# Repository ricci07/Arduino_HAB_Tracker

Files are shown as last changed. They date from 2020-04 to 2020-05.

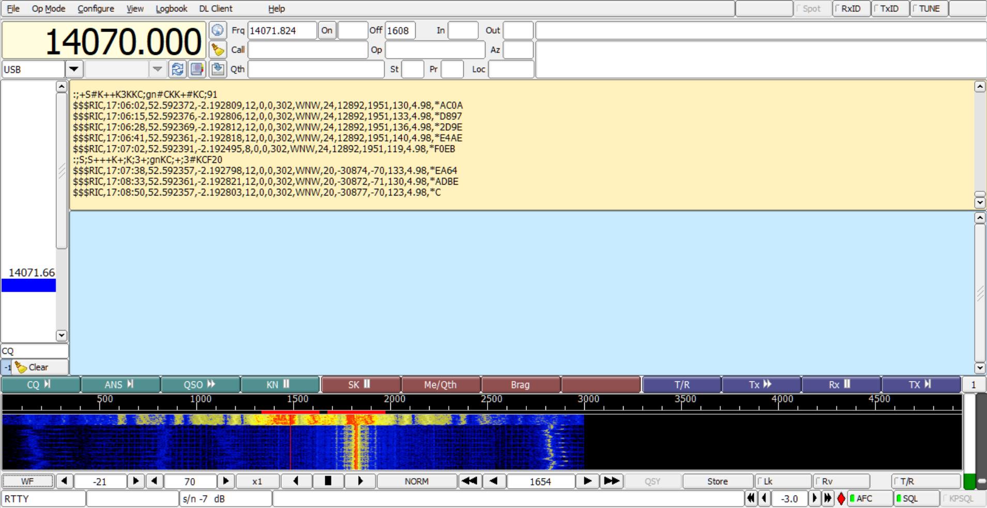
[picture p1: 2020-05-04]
Screenshot/Thesis/DL-Fldigi showing RTTY lesser unwanted tone oscillation when connected to external 3V with external ground and arduino ground linked.jpg

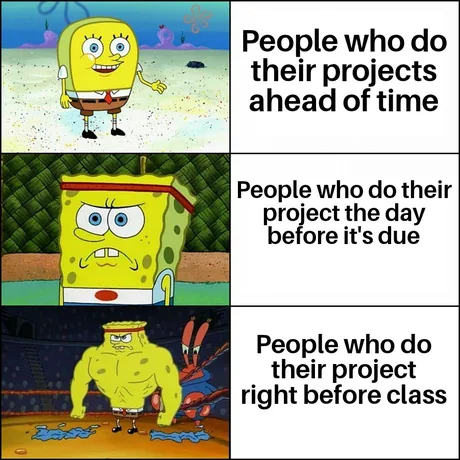
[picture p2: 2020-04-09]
Proposal/project.webp

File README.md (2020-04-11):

# Arduino_HAB_Tracker
Undergraduate Dissertation HAB Telemetry Development

This is a HAB tracker PCB I am making for my final year project based on information provided by the UKHAS (society)
I am building this from breakout boards, which is not my preferred solution, but it will speed up developement 10-fold (I don't have the time for anything pretty right now)

It features an Arduino UNO (clone), Ublox-M8Q (GPS) Radiometrix NTX2B, BH1750 (light sensor), BMP280 (pressure sensor), ML8511 (UV sensor), MPU-9250 (9 Axis Sensor, 3D acc, 3D GYR, 3D Mag), MS5611 (Super-high alitude sensor), and voltage sensor (this consists of a voltage divider so many be implemented directly)

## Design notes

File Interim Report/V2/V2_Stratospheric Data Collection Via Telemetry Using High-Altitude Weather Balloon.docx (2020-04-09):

# Stratospheric Data Collection via Telemetry Using High-Altitude Weather Balloon

Interim Report

by Riccardo Geraci

Friday, 24 January 2020

# 1 Abstract

Weather balloons are an invaluable tool used professionally by meteorology organisations for collecting various types of atmospheric data used in forecasting the weather. This includes collecting things such as atmospheric pressure, humidity, and temperature. Outside of the professional sector they are highly used by radio amateurs to gather sensor data and photos and videos of the Earth’s curvature. The types of sensor data commonly collected by amateurs are from a 3-axis accelerometer, 3-axis gyroscope, 3-axis magnetometer, relative humidity, altitude, temperature, pressure, ambient light, and ultraviolet light. These are then transmitted to ground via the onboard telemetry via the 70cm 434MHz HAM band to a computer connected to a radio receiver, DVB-T dongle, Funcube+ dongle, or airspy which is tuned to 434Mhz. The main tracking computer is usually run inside a chase car with a magnetically mounted 70cm band antenna. The GPS location of the balloon is broadcasted the same way as the sensor data with the coordinates acquired from an onboard GPS module connected to low orbit satellites. A service called habhub is used by the majority to allow anyone around the world to track the balloon. This has the advantage of filling in any signal loss you may encounter since someone else is relaying the coordinates to the server for you. Balloons of various sizes, commonly between 300-600g for first time launchers ascend until a point (usually 60,000-120,000ft depending on the balloon size, with larger more expensive ones achieving higher altitudes) where the air pressure is so low (about 0.1 atmospheres) which causes the balloon to expand until rupturing. At this point the payload containing the electronics descend with a legally required parachute somewhere near a previously software predicted landing location. This is commonly between 2-3 hours away from the launch location. Lots of preparation is done to ensure the prediction is not in the ocean. Though prediction algorithms aren’t perfect, and the weather has tendency to change unpredictably so the landing location prediction needs constant rerunning to ensure the most updated location is known.

Ukhas.org (UK high altitude society) is the single most abundant and reliable source of high-altitude ballooning on the internet with veteran members creating articles which instruct others how to launch a balloon of their own. These members have been approached by organisations such as the BBC to fabricate and launch balloons for TV and have helped myself in this project with direct correspondence or through their articles. Credit will be paid to them where appropriate in interim or dissertation. Without their contributions this project would have not been possible to carryout due to its complexity.

# 2 Introduction

# 3 Design Constraints

## 3.1 Altitude

The burst altitude is dependent on various factors such as the size of the balloon, payload weight, and rate of ascent. Common 600g Totex balloons have a burst altitude of between 75,000 - 90,000ft whereas larger and more expensive balloons (800g-4000g) have a larger gas capacity and extended amount of stretch than smaller ones (100-600g). So, they have a longer time of ascent, hence altitudes of beyond 90,000ft can be achieved (Kaymont.com, 2020). For this project a 600g will be used as it is the most commonly used latex balloon for first time launchers and can be purchased from Steve Randall’s website; randomengineering.co.uk for ≈£25

## 3.2 Launch

In the UK, permission must be obtained prior to launch from the Civil Aviation Authority (CAA) before any weather balloons can be launched. An OS map pinpointing the planned launch location must be sent before permission is granted. If valid, permission and a NOTAM (notice to airmen) will be issued. Due to unpredictable weather a window of different launch dates should be requested. 28 days prior notice must be given before planned launch date (Stirk, 2012).

## 3.3 Location

## 3.4 Software Defined Radio

Software defined radio is an inexpensive alternative to using an expensive but also more sensitive radio such as the most commonly used Yaesu 817. SDR dongles utilise the Realtek RTL2832U chipset and computer’s soundcard to decode radio signals. However, SDR dongles are repeatedly discouraged for tracking actual balloon flights due to their reduced sensitivity when compared to a proper radio. Although, this argument is conflicted by different people and a compromise has to be taken.

## 3.5 Tracking

After launching of the balloon, a chase car with a magnetically roof mounted 70cm band antenna connected with a length of SMA terminated RG174 cable is fed to and usb dvb-t dongle connected to a computer running sdrsharp software tuned to ≈ 434.425MHz, the same as the payload transmitting frequency. The received RTTY tones are then sent to dl-fldigi software via a virtual audio cable where the tones are decoded in sentences containing the GPS coordinates of the balloon’s current position. This GPS information is then relayed to habhub to allow worldwide tracking of the balloon (Stirk, 2012).

## 3.6 Flight Computer

Original plans were to use the raspberry pi as per mentioned by Heather Lomond Ph.D, a member of TDARS amateur radio group I attended as per suggestion of Mohammad Sayed. The raspberry pi allows the use of the pi camera which could have programmed to take photos every x seconds. Heather has launched two weather balloons before and shared her story of how she achieved it. She mentioned she used the pi-in-the-sky flight tracker developed by Dave Akerman. This is a tracker that is pre-made by one of the expert HAB members to slot on the top of raspberry pi. However, due to price of £144, an ambitious decision to develop my own flight tracker was made.

## 3.7 GPS

The GPS module chosen for this project is the uBlox Max-M8Q. This is the most commonly used GPS chip used by the HAB community because it continues to operate up to 50,000 meters when in flight mode. Not all GPS modules continue to work at this altitude and result in monotonic values. This ensures the balloon’s location doesn’t go silent when the balloon goes beyond the operating altitude (uBLOX MAX-M8Q Breakout for Active Antennas, 2016).

## 3.8 Balloon

A 600g Totex balloon from randomengineering.co.uk is going to be used to carry a payload of 500-900g

## 3.9 Size

## 3.10 Payload

## 3.11 Gas

## 3.12 Transmitter

## 3.13 Parachute

## 3.14 Power Supply

## 3.15 Regulations

## 3.16 CAA Limitations

## 3.18 SDR

## 3.19 Budget

## 3.20 Sensors

## 3.21 9 Axis Sensor

## 3.22 Talk about the 3 axis acceleraomter, 3 axis gyroscope, and 3 axis magnometer.

## 3.23 Ambient Light Sensor (GY-302)

## 3.24 Talk about how the light sensor will be used to record the light level increase/decreate during the flight of the ballon

## 3.25 UV Light Sensor (GY-8511)

## 3.26 Talk about how the light sensor can track the uv levels during ascent and decent which we can parse the data to create graphs in excel

## 3.27 Altitude Sensor & 9 Axis Sensor (MS5661 & MPU-9250)

## 3.28 Talk about how the bmp280 stop function beyond certain altitude (60,000ft/10hPa), but the MS5661 works up to 100,000ft/ 1hPa which is required to allow for no monotonic values beyond that point

## 3.29 Voltage Sensor

## 3.30 Talk about how the voltage sensor can be used to monitor the battery percentage and so that we can look at how to battery level went down during the flight of the balloon.

## 3.31 Printed Circuit Board (PCB)

# 4 References

Kaymont.com. (2020). [online] Available at: https://www.kaymont.com/product-page/hab-600 [Accessed 24 Jan. 2020].

Stirk, A. (2012). general:restrictions_legality [UKHAS Wiki]. [online] Ukhas.org.uk. Available at: https://ukhas.org.uk/general:restrictions_legality [Accessed 24 Jan. 2020].

Stirk, A. (2012). guides:sdr_tracker [UKHAS Wiki]. [online] Ukhas.org.uk. Available at: https://ukhas.org.uk/guides:sdr_tracker [Accessed 24 Jan. 2020].

uBLOX MAX-M8Q Breakout for Active Antennas. (2016). [ebook] Bingley: uputronics, p.2. Available at: https://store.uputronics.com/files/HAB-BO-M8Q3A-ASSY.pdf [Accessed 24 Jan. 2020].

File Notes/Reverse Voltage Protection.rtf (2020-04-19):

Reverse Voltage Protection

There are many ways to provide voltage protection to a circuit

• Series diode after power source (Basic, not great, alot of wasted heat)

• Series shotkey diode after power source (Better, less heat wasted but still not the ultimate method). A shotkey diode has a lower forward voltage.

• P-channel mosfet with Drain conected in series with the positive supply and the source connected to the load (Absolute best way)

Wasted heat calculation

Forward Voltage x Current = Wasted Power

How much is too much wasted heat?

Anything approaching 2W is on the high side.
A max of 1W or below is preferrable.

Which diode?

P/N 1N4001 [1]

Which Shotkey diode?

P/N MBRA130 [1] or STPS2L60 (0.55V forward voltage) [2]

Which P-channel Mosfet?

FQP47P06 [2]
• Pay attention to the unconvention pin configuration of this mosfet

How to wire the p-channel mosfet [2]
• The drain-source voltage rating must be higher than the psu voltage [2]
• Rds(on) should be as low as possible to minimize the resitive power losses [2]
• Get one with a high gate-source voltage (+-25v) [2]

• The mosfet is parasitic so there is a 1V volt-drop across (D)rain and (S)ource [2].
• This means the (S)ource pin is at 11V w.r.t GND [2]
• The gate voltage is 0V because it is connected to GND [2]

How to deal with voltages higher than gate-source voltage range
• Use a resistor and zener diode (1N5240) (10V) in this configuration [2]
• A zener between 6-12V should be adequate [2]

References

[1] https://www.allaboutcircuits.com/technical-articles/how-to-protect-your-circuits-using-only-a-diode/

[2] https://www.youtube.com/watch?v=IrB-FPcv1Dc

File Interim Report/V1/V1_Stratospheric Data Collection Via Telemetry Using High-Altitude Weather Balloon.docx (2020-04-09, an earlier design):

# Stratospheric Data Collection via Telemetry Using a High-Altitude Weather Balloon

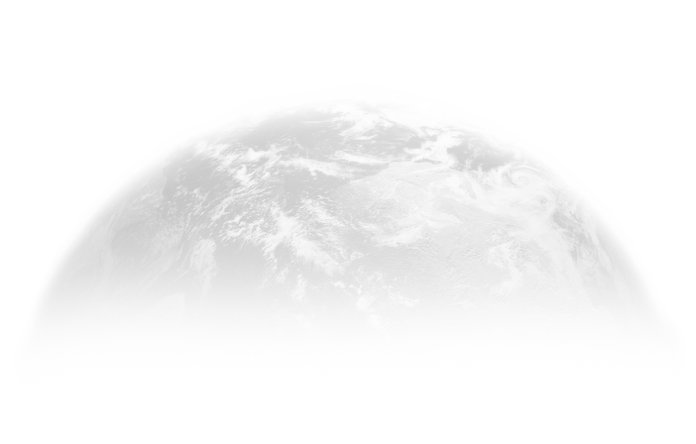
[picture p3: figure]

Interim Report

by Riccardo Geraci | 1615626

Friday, 14 February 2020

Supervised by Niki Zakeri

# 1 Abstract

Weather balloons are an invaluable tool used professionally by meteorology organisations for collecting various types of atmospheric data used in forecasting the weather. This includes collecting things such as atmospheric pressure, humidity, and temperature. Outside of the professional sector, they are highly used by radio amateurs to gather sensor data, photos, and videos of the Earth’s curvature.

The types of sensor data commonly collected by amateurs are via 3-axis accelerometers, 3-axis gyroscopes, 3-axis magnetometers, relative humidity sensors, pressure/altitude sensors, temperature sensors, ambient light sensors, and ultraviolet light sensors. These are then transmitted to the ground by telemetry via the 70cm 434Mhz HAM band to a computer connected to a radio receiver, DVB-T dongle, FUNcube Pro+ dongle, or Airspy – which is also tuned to 434Mhz with SDR tuning software in the case it’s a DVB-T dongle. The main tracking computer is typically running from inside a chase car with a magnetically roof-mounted 70cm band antenna. The GPS location of the balloon is transmitted the same way as the sensor data but with the coordinates acquired from an onboard GPS receiver connected to GPS satellites.

A service called HABhub is used by UKHAS to allow anyone around the world to track the balloon. This has an advantage of filling in any signal loss encountered by someone else relaying the GPS coordinates to the server.

Balloons of various sizes, commonly between 300-600g for first-time launchers, ascend at an ideal 5m/s until a point (usually 60,000-120,000ft depending on the balloon size and system mass, with larger and more expensive balloons achieving higher altitudes) where the air pressure is low enough (about 0.1 atmospheres) that the balloon expands to the point of rupturing. For a 600g balloon, this is 6.5m in diameter (Randall, 2019). For the best photographs of the Earth, an altitude of 25-30km/82,000-98,000ft is an ideal altitude to aim for (Akerman, 2015).

Following the balloon bursting, the payload containing the electronics descend with a legally required parachute at an ideal descent rate of 5m/s tuned by the size of the parachute selected, somewhere near a previously software predicted landing location. This is commonly between 2-3 hours away from the launch location. Lots of preparation is done to ensure the prediction is not in the ocean, airport, or restricted areas. Though prediction algorithms aren’t perfect, and the weather tends to change unpredictably, so the landing location prediction needs constant rerunning to ensure the most updated location is known.

From running several prediction tests, the average flight until the balloon bursts is usually 90-100 minutes, with a flight duration of approximately 120-130 minutes. See 3.12 - Provisional Flight Prediction to see information about this in more detail.

# 2 Introduction

This interim report introduces some of the research carried out from October 2019 to January 2020 in the development of a high-altitude weather balloon for obtaining sensor data from the stratosphere. The research includes learning how to build a flight tracker by interfacing a uBlox GPS chip with a microcontroller via UART serial and parsing the NMEA sentences and extracting the desired GPS coordinates and altitude. The tracker also includes a Radiometrix NXT2B which transmits the relevant sentences via traditional RTTY to the receiver antenna mounted on top a chase car. Other data protocols such as CW (Morse), DominoEX, and LoRa are also used instead of or in conjunction with RTTY and live in-flight images can be sent with SSTV (Coxon, 2020).

The majority of the research has come from Ukhas.org (UK high altitude society). They offer the single most abundant and reliable source of high-altitude ballooning on the internet with veteran members creating articles which instruct others how to launch a balloon of their own. These members have been approached by organisations such as the BBC to fabricate and launch balloons for TV and have helped directly in this project with one-to-one correspondence or through their public articles. Credit will be paid to them where appropriate in interim or dissertation. Without their contributions, this project would have not been possible to carry out due to its complexity.

The sensor modules were purchased in breakout board form with the intention of integrating them into a tracker PCB containing the other key components such as the Radiometrix NTX2B, SMA antenna connectors, and switch-mode voltage regulators. All the sensor boards use I2C to communicate with the microcontroller, which means the SDA and SCL lines will need to be interconnected with a BUS to pins A4 and A5 of the Arduino.

Switched-mode voltage regulators will be used to supply the various voltages from an external source required by the different sensors, such as 3.3v and 5v without putting too much strain on the Arduino supply.

The research into the parachute required, helium amount required, and which chase car antenna is required has been pushed towards the end of the research as it is dependent on the totals of other components. To ensure the correct parachute size is purchased or fabricated, the total mass of the system will need to be measured first to acquire an optimal descent rate/landing speed of 5m/s (Akerman, 2015).

To ensure to correct helium quantity is obtained, the system mass, balloon size, and target burst altitude/ascent rate need to be determined first. The parachute size can be determined once the system mass is measured.

# 3 Design Research

## 3.1 Budget

The budget for this project has been more expensive than anticipated. Many technical articles have quoted £200, which is quite underestimated. As of 26/01/20, not all items have been purchased and ≈ £300 has already been spent. After purchasing the remaining items, such as helium, laptop inverting charger, parachute, action camera, SD card, mag-mount antenna, and balloon, the expenses come to £498.55. This excludes ≈ £40 fuel costs to retrieve the payload upon landing 2-4 hours away depending on the effects of wind on the day of launch. Appendix A – Parts List and Project Budget shows the currently spent funds in obtaining the necessary equipment and parts.

## 3.2 Altitude

The burst altitude is dependent on various factors such as the size of the balloon, payload weight, and rate of ascent. Common 600g latex balloons have a burst altitude of between 75,000ft - 90,000ft (Kaymont.com, 2020) whereas larger and more expensive balloons (800g-4000g) have a larger gas capacity and extended amount of stretch than smaller ones (100g-600g). So, they have a longer time of ascent, hence altitudes of beyond 90,000ft can be achieved (Kaymont.com, 2020). For this project, a 600g-1000g balloon will likely be used as they are the most commonly used latex balloons for first-time launchers and can be purchased from Steve Randall’s website; randomengineering.co.uk for ≈£25

## 3.3 Launch

In the UK, permission must be obtained prior to launch from the Civil Aviation Authority (CAA) before any weather balloons can be launched. An OS map pinpointing the planned launch location must be sent before permission is granted. If valid, permission and a NOTAM (notice to airmen) will be issued. Due to unpredictable weather, a window of different launch dates should be requested. 28 days prior notice must be given before the planned launch date (Stirk, 2012).

## 3.4 Software Defined Radio

Software-defined radio is an inexpensive alternative to using an expensive but also more sensitive radio such as the most commonly used Yaesu 817. SDR dongles utilise the Realtek RTL2832U chipset and computer’s soundcard to decode radio signals. However, SDR dongles are repeatedly discouraged for tracking actual balloon flights due to their reduced sensitivity when compared to a proper radio. Although, this argument is conflicted by different opinions and a compromise has to be taken.

## 3.5 Tracking

After launching of the balloon, a chase car with a magnetically roof-mounted 70cm band antenna connected with a length of SMA terminated RG174 cable is fed to a USB DVB-T dongle connected to a computer running SDRsharp software tuned to ≈ 434.425MHz, the same as the payload transmitting frequency. The received RTTY tones are then sent to dl-fldigi software via a virtual audio cable where the tones are decoded character by character into sentences containing the GPS coordinates of the balloon’s current position. This GPS information is then relayed to HABhub to allow worldwide tracking of the balloon (Stirk, 2012). Once the balloon lands, the perfect line of sight is almost always lost, and usually the signal with it. It is recommended to use a YAGI antenna from this point since they are highly directional and can detect faint signals (Akerman, 2015). It’s best to drive around the predicted landing location with a YAGI antenna until the signal is re-established to locate the payload (Lomond, 2019).

## 3.6 Flight Computer

Original plans were to use the Raspberry Pi as per mentioned by Heather Lomond PhD, a member of TDARS amateur radio group recommended by Mohammad Sayed. The Raspberry Pi allows the use of the Pi camera which could have programmed to take photos every x seconds. Heather has launched two weather balloons before and shared her story of how she achieved it. She mentioned she used the pi-in-the-sky (PITS) flight tracker developed by Dave Akerman and Anthony Stirk. This is a tracker that is pre-made by two expert HAB members to sit on the top of the Raspberry Pi. However, due to the price of £144, an ambitious choice to develop a flight tracker was made.

A later decision came to switch to the Arduino since the Raspberry Pi in a UKHAS member’s own words is ‘hardly ideal as a flight controller’ due to requiring knowledge of running a real-time kernel, linking a c program, higher power consumption (5-10 times more than normal tracker), and has a limited about shields readily available, etc (Akerman, 2020). Most of the available sample code for GPS and RTTY transmission is written for Arduino and is difficult to reimplement in python for the Raspberry Pi without significant python knowledge.

## 3.7 GPS

The GPS module chosen for this project is the uBlox Max-M8Q. This is the most commonly used GPS chip used by the HAB community because it continues to operate up to 50,000 meters when in flight mode. Not all GPS modules continue to work at this altitude and result in monotonic values. This ensures the balloon’s location doesn’t go ‘silent’ when the balloon goes beyond the operating altitude (uBLOX MAX-M8Q Breakout for Active Antennas, 2016).

## 3.8 Balloon

A 600g Latex balloon from randomengineering.co.uk is going to be used to carry a payload of between 500g and 900g. The payload will need to carry 4-6 lithium AA batteries that serve as the power supply, microcontroller, tracker/sensors PCB, action camera, etc. The weight of the payload container, which is a 2.4L polystyrene box, parachute, connecting lines, and antenna, needs to be accounted for in the lifting capabilities of the balloon. The balloon has a burst diameter of 6.5m which is significantly larger than its diameter at launch (Randall, 2019).

Helium will be used as the lifting gas. It’s the most commonly used gas in HAB because it is safer to use than hydrogen and methane. Though hydrogen is cheaper and lighter (hence, has more lift) it is said to be explosive when mixed with the correct amount of air. Although, hydrogen also does not diffuse out of the balloon as quickly as helium (Coxon, 2009).

The Radiometrix NTX2B 434.425MHz 10mW transmitter is the proven workhorse of many trackers used by the HAB community. In fact, 10mW is the maximum operating power that can be used for licence-free transmission. This still allows several hundreds of miles of signal due to a perfect line of sight to the receiver when in the sky (Coxon, 2009). The transmitter is connected to a 50 Ω RG174 pigtail via an SMA connector. The antenna radiating element is cut to 164mm to achieve a ¼ wave. A 4-point radial of approximately 164mm is used to simulate a ground plane or counterpoise to increase the reflections of the radio signal (Coxon, 2014).

## 3.9 Parachute

The parachute is a requirement by the CAA to bring the payload and balloon remnants back to the ground safely. The size of parachute depends on the balloon’s post burst weight. Parachutes can be found cheaply ( ≈ £25), expensively ( ≈£65) , or can be made at home using a sewing machine and nylon sheeting. Nylon is used for its strength and resistance to the cold since the temperature in the stratosphere averages at about -50 ℃ (Coxon, J, 2009).

The balloon train must also be made of nylon, usually, 1mm braided as this provides enough strength but has a low enough breaking strain as required by the CAA (Lomond, 2019). 1mm braided nylon has a breaking strain of about 22.5KG/220N, however, it is not made to precise breaking strain (Randall, 2019).

## 3.10 Power Supply

The source of power for this purpose is to use disposable energiser lithium AA batteries as they are the most resilient to the cold ( -40^o C to +60^o C ) (Energizer, n.d.) and are energy-dense. 6 x 1.5V AA lithium will provide a 9V power supply which is expected to last around 5 hours when coupled with an appropriate switched-mode voltage regulator. However, this will depend on the total current draw from the components, which can be evaluated after the construction of all circuitry for a more accurate expected working time (Coxon, 2009). Adding another 6 in parallel will double the working time to about 10 hours (Akerman, 2015).

## 3.11 Sensors

The objective of launching a high-altitude balloon was to collect data from several different sensors aboard the payload. The original intention was to gather atmospheric pressure, altitude, and temperature. But since meeting with Heather Lomond, who showed off the graphical results of her flights, several breakout boards were purchased with the intention of integrating them into a larger PCB which is connected to the microcontroller. This will include a 3-axis accelerometer, 3-axis gyroscope, 3-axis magnetometer, ambient light sensor, UV light sensor, altitude/pressure sensor, voltage sensor, internal temperature sensor, and external atmospheric temperature sensor. As of 24/01/20, most of these sensors have been tested within Arduino code and suitable library and appear to provide valid readings. The library code of some of these sensors has also been studied to understand how the internal registers are set to configure the different operating modes of the chips. A detailed explanation of how these library operations work will likely be included in the thesis.

## 3.12 Provisional Flight Prediction

Calculations were made to test the prediction algorithms that will be used during the actual launch. Note: the below flight landing prediction is only valid for if the launch were to happen on 30/01/20 and will be completely unusable for the real launch several months in the future.

Figure 1- Provisional Flight Predictions for 30.01.20 Using predict.habhub.orgFigure 1 shows the hypothetical predicted flight path for a balloon launch from Priorslee, Telford at 8 am on 30/01/20. The burst altitude is supplied using a balloon burst calculator as 29,485m/96,735ft. The ascent and descent rates are left as the default ideal 5m/s. Notice how the flight path is influenced by the jet stream.

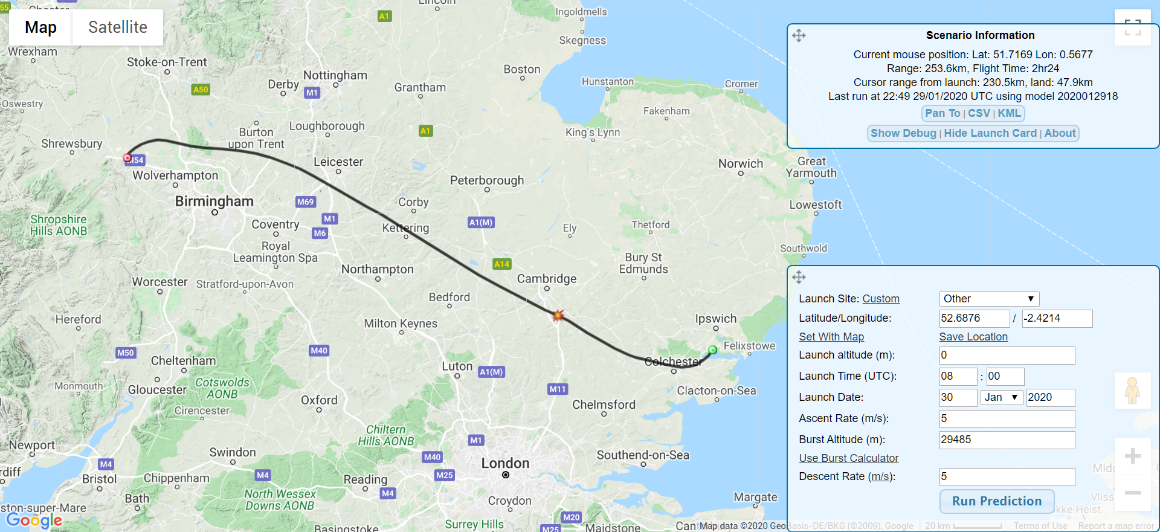
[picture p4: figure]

Landing

Launch

Burst

Figure 1- Provisional Flight Predictions for 30.01.20 Using predict.habhub.org (Geraci, 2020)

If this was treated as a real launch prediction, the launch would be postponed until the landing location prediction was further away from the North Sea.

## 3.13 Provisional Balloon Calculation

Figure 2 shows the resulting key information if a payload mass of 900g (including the braided nylon cord and parachute) was launched with a Hwoyee 600g balloon with a nominal recommended ascent rate of 5m/s.

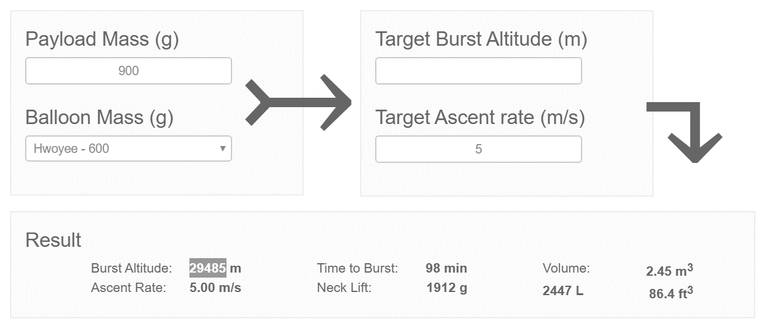
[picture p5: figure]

Figure 2 - Balloon Burst Calculation Using habhub.org/calc/ (Geraci, 2020)

This gives the estimated burst altitude of 29,485m/96735ft which is then passed in as the burst altitude in Figure 1. It also shows the neck lift, which is how much lift the balloon has when filled with 2.45 m^3 of helium (Akerman, 2015). The majority of balloons require less than 3.6 m^3 of helium which comes as a BOC type ‘T’ costing approximately £100 (Akerman, 2015). The amount of helium required should not typically go beyond 3.6 m^3 as this will requite a much larger cylinder, with a more expensive price.

## 3.14 Provisional Time-lapse Calculation

An action camera aboard the payload will be used to capture a 1-2s interval time-lapse of the balloon’s ascent and descent. Time-lapse is preferred over a continuous 4k video as the camera will not consume as much power and will speed up the balloon’s slow ascent and descent. Figure 3 shows the storage required if an 8MB image is captured every 2s, with an output of 24FPS. The clip length will be 3 minutes, with 33.75GB of 64GB used. The number of photos should be 4,320. 64GB is the maximum micro SD card size the action camera will accept.

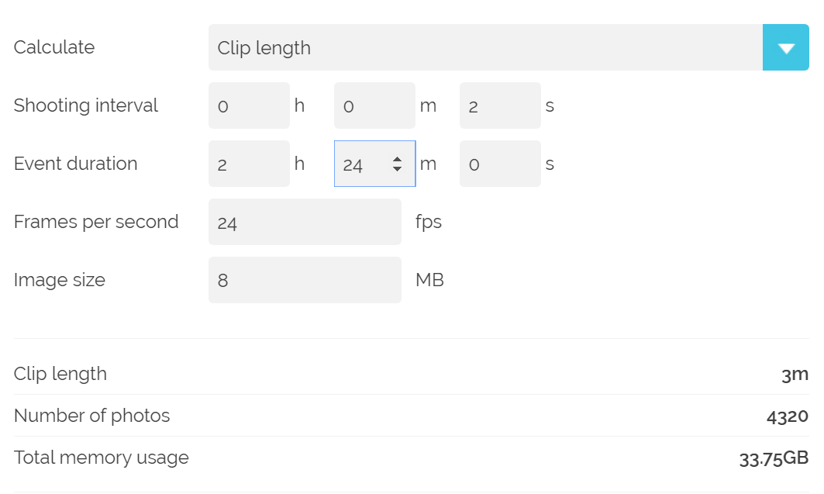
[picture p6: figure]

Figure 3 - Time Lapse Showing Results of Time Lapse Using photopills.com/calculators/timelapse (Geraci, 2020)

Manually calculating the time-lapse:

i=t/(F/L)

Where i = interval, t = event duration (in seconds), F = 30, L = playback length (in seconds)

i=t/(FL)

iFL=t

t=1×30×(5×60)

t=2.5 hours

This means to achieve a time-lapse of 5 minutes long at 30 FPS, an interval of 1s would be required over the course of 2.5 hours.

## 3.15 Configuration

GPS Satellite

28dbi 1575.42 Mhz GPS Patch Antenna

Ublox Max-8 Breakout Board

Arduino Microcontroller

Radiometrix NTX2B 434.425 Mhz 10mw

UART Serial

1575.42MHz

High/Low Beeps Program Output

3-Axis Accelerometer

3-Axis Gyroscope

3-Axis Magnetometer

Pressure/Altitude

Internal Temperature

External Temperature

Ambient Light

UV Light

Voltage

Sensor Module Outputs

6x1.5V Lithium-Ion AA Power Supply

I2C/SPI

Chase Car

RTTY

Mag-Mount 70cm Band Whip Antenna

164mm RG174 ¼ Wave Antenna With 4-Point Radial

DVB-T Dongle

Laptop Running SDRsharp & dl-fldigi

USB

Laptop Cigarette Lighter Inverting Power Supply

Mobile Hotspot

Habhub

GPS Data

Time Lapse Action Cam

3V/5V

5V

3V

Figure 4- Telemetry Configuration of Balloon (Geraci, 2020)

## 3.16 CAD Model

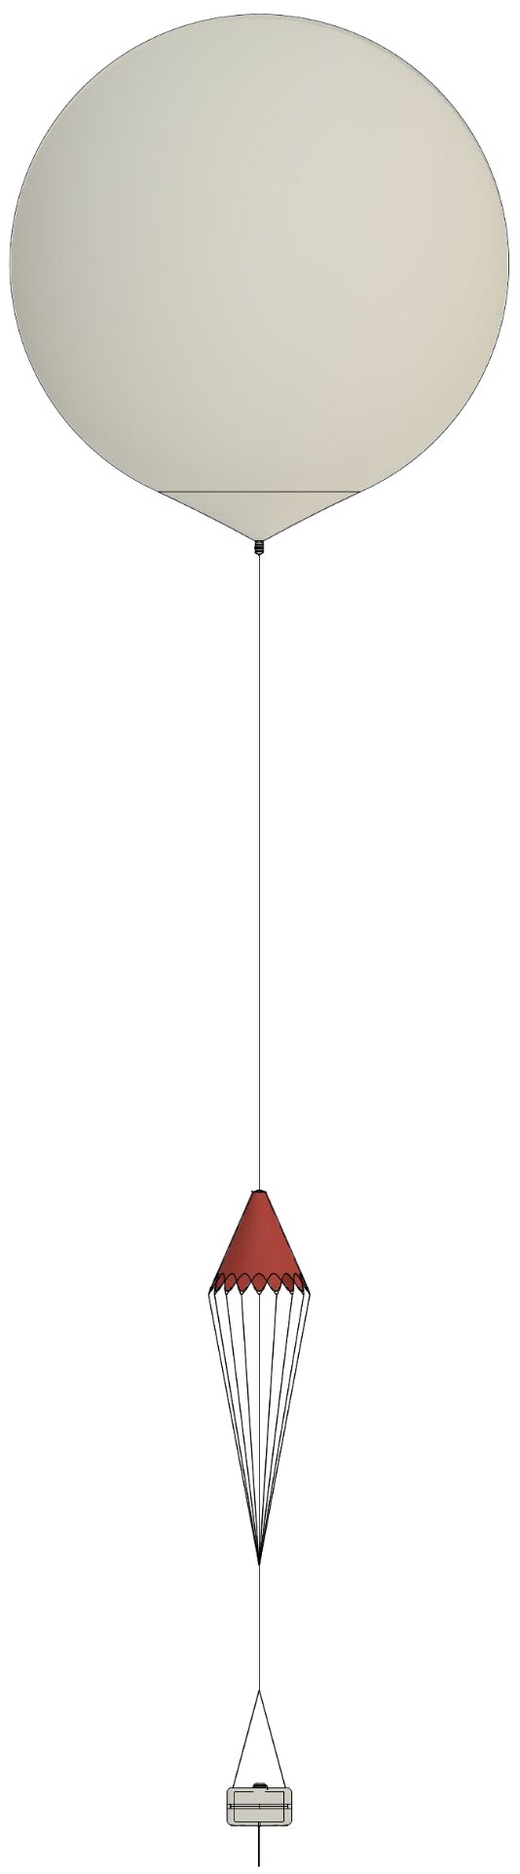
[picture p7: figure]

164mm ¼ RG174 to SMA Pigtail Antenna

2.4L Polystyrene Payload

600g Latex Balloon (6.5m burst diameter) (TBC)

36” Parachute (to be confirmed by calculation)

5m 1mm Braided Nylon Nylon

Figure 5 - CAD Model Drawing of Balloon (Geraci, 2020)

5m 1mm Braided Nylon

5m 1mm Braided Nylon

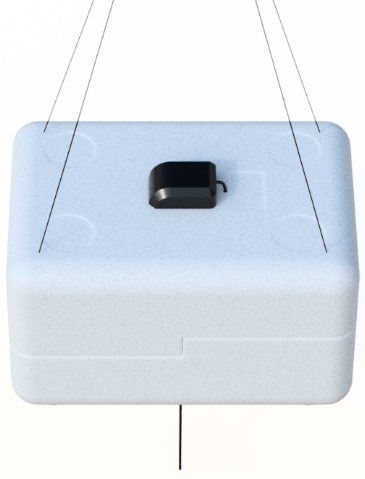
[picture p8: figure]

Figure 6 - Top View of Payload Showing GPS Patch Antenna (Geraci, 2020)

Payload (Top)

4-Point Radial (Equipment Wire) to Simulate a Ground Plane

2.4L Polystyrene Container

28dBi GPS Patch Antenna

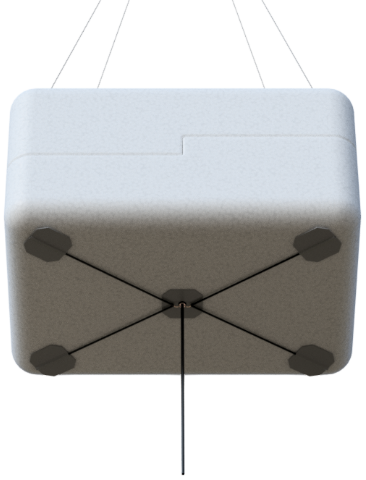
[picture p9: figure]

Figure 7 - Bottom View of Payload Showing 164mm 1/4 Wave Transmitter Antenna (Geraci, 2020)

Payload (Bottom)

164mm RG174 to SMA Payload Antenna

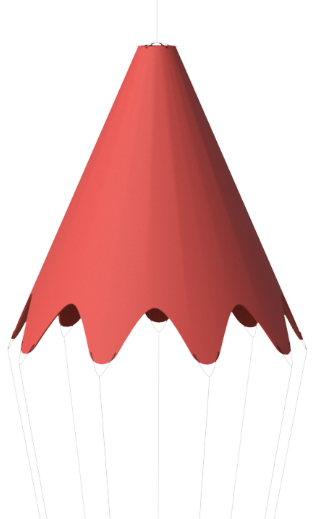
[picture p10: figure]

Figure 8 - Parachute (Geraci, 2020)

Parachute

36” Pre-deployed Parachute (Actual size to be determined later)

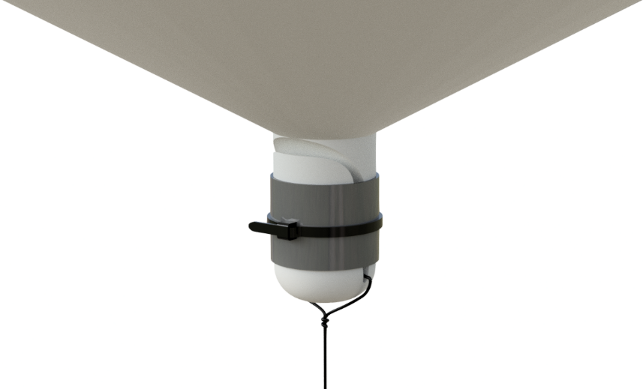
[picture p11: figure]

Figure 9 - Neck of Balloon Showing Attachment of 1mm Nylon Cord (Geraci, 2020)

Balloon (Neck)

Hangman’s Knot

Balloon Neck & 1mm Braided Nylon Connection with Duct Tape and Cable-Tie

# 4 Further Work Required

There is still a lot of work to be carried out in order to complete the project, with the most important areas listed below.

- Design of sensor module/flight tracker PCB hat/shield for Arduino/microcontroller
- Find out how to use the MS5661 pressure sensor to determine altitude
- Learn how to parse GPS NMEA sentences to extract GNGGA and GPRMC data
- Successfully transmit and receive parsed GNGGA and GPRMC sentences with NXT2B
- Write a program to encode and transmit GNGGA, GPRMC, and sensor data as RTTY sentences
- Determine how to relay received GPS coordinates from dl-fldigi to HABHUB
- Alert other balloonists of my launch plans
- Create 164mm ¼ wave payload antenna from RG174 to SMA pigtail
- Purchase action camera to mount inside payload to capture time-lapse of flight
- Purchase 70cm band mag-mount antenna
- Run lots of tracking tests upon completion of tracker
- Calculate, and purchase the actual balloon size required
- Calculate the actual helium amount required and find a reliable helium renting service
- Calculate, and purchase the actual size of parachute required for a landing speed of 4-5m/s
- Create a suitable power supply using a switched-mode voltage regulator(s)
- Fabricate a fill tube for inflating the balloon
- Estimate balloon true burst altitude, burst time, flight time, landing time and power supply end-time
- Purchase a laptop inverting charger to allow balloon tracking in the chase car
- Run landing location predictions frequently a week up to launch, and repeatedly after launch
- Determine a suitable launch location
- Apply for launch permission and NOTAM from CAA 28 days prior to launch
- Determine the essential kit required on the day of launch day
- Arrange for a driver to chase the balloon landing location

# 5 Conclusion

Choosing a high-altitude balloon as a final year university project sounds simple to the inundated. While it isn’t exactly ‘rocket science’, it’s not so easy such that anyone could accomplish it either. Especially if the decision is taken to design a flight tracker themselves to save money. If one doesn’t have any experience in programming or electronics, it’s almost impossible to do without any experienced intervention. Even for the fairly experienced coder, the transmission code, NMEA parser code can be quiet a learning curve to understand. If one doesn’t know the concept of start bits, checksums, stop bits, parity, etc it can be quite cryptic.

Luckily, ballooning can be done with a modest budget of between £200-£500 which has made it accessible to many hobbyists which have helped create articles on how to design trackers, write code, and everything else required to launch successfully. However, all the available information is found in isolation, and combining it all into a working tracker is something of a challenge to figure out independently.

Contact was made with Steve Randall, director of randomengineering.co.uk, regarding this project. He offered helpful advice, on what should be omitted, how antennas should be created and what payload container to use. He runs the site where balloons and parachutes are acquired by UK balloonists.

Heather Lomond PhD, of TDARS group, offered her experience in launching high-altitude balloons. She gave a lot of information and advice via email about how she achieved her launches.

To finish this project, as discussed in 4 - Further Work Required, the GPS strings need to be parsed to extract useful information such as the latitude, longitude, and altitude. These strings need to be encoded with RTTY transmission code, transmitted to the SDR, and decoded with dl-fldigi.

The flight tracker needs to be designed so that it utilises the Radiometrix NXT2B, sensor breakout boards, SMA connectors, power connectors, voltage regulators and external temperature probe. It also needs to slot directly on top of the Arduino header pins and secured.

Experimental tests will be carried to ensure the tracker works as expected and the transmissions are detected across long distances. Once these have been confirmed, the balloon’s mass will be measured to ensure the correct balloon size and gas quantity is obtained.

Once all physical materials are satisfactory, contact to the CAA will be made to request a NOTAM for several weekends in the following month. After this has been arranged, a kit required on launch day will be devised to ensure items such as scales, tarps, water, bottles, scissors etc are taken to the launch site.

A suitable driver will be asked to drive the chase car towards the predicted landing location so that the tracking of the balloon can be handled by the owner of the project.

# 6 References

Akerman, D. (2015). High Altitude Ballooning, From The Ground Up (and back again) | Dave Akerman. [online] Daveakerman.com. Available at: http://www.daveakerman.com/?p=1732 [Accessed 2 Feb. 2020].

Akerman, D. (2020). guides:raspberrypi [UKHAS Wiki]. [online] Ukhas.org.uk. Available at: https://ukhas.org.uk/guides:raspberrypi [Accessed 2 Feb. 2020].

Coxon, J. (2009). general:beginners_guide_to_high_altitude_ballooning [UKHAS Wiki]. [online] Ukhas.org.uk. Available at: https://ukhas.org.uk/general:beginners_guide_to_high_altitude_ballooning [Accessed 2 Feb. 2020].

Energizer. (n.d.). Energizer® Ultimate Lithium Batteries - AA, AAA & 9V. [online] Available at: https://energizer.eu/uk/blog/product/energizer-ultimate-lithium-aa/ [Accessed 4 Feb. 2020].

Kaymont.com. (2020). [online] Available at: https://www.kaymont.com/product-page/hab-600 [Accessed 24 Jan. 2020].

Kaymont.com. (2020). [online] Available at: https://www.kaymont.com/habphotography [Accessed 24 Jan. 2020].

Lomond, H. (2019). High Altitude Balloons. [email].

Randall, S. (2019). Balloons. [online] Randomengineering.co.uk. Available at: http://randomengineering.co.uk/Random_Aerospace/Balloons.html [Accessed 2 Feb. 2020].

Randall, S. (2019). HAB Stuff. [online] Randomengineering.co.uk. Available at: http://randomengineering.co.uk/Random_Aerospace/Stuff.html [Accessed 2 Feb. 2020].

Stirk, A. (2012). general:restrictions_legality [UKHAS Wiki]. [online] Ukhas.org.uk. Available at: https://ukhas.org.uk/general:restrictions_legality [Accessed 24 Jan. 2020].

Stirk, A. (2012). guides:sdr_tracker [UKHAS Wiki]. [online] Ukhas.org.uk. Available at: https://ukhas.org.uk/guides:sdr_tracker [Accessed 24 Jan. 2020].

uBLOX MAX-M8Q Breakout for Active Antennas. (2016). [ebook] Bingley: uputronics, p.2. Available at: https://store.uputronics.com/files/HAB-BO-M8Q3A-ASSY.pdf [Accessed 24 Jan. 2020].

Ukhas.org.uk. (2014). guides:payload_antenna [UKHAS Wiki]. [online] Available at: https://ukhas.org.uk/guides:payload_antenna?rev=1417961645 [Accessed 2 Feb. 2020].

# 7 Appendix

## 7.1 A – Parts List and Project Budget

Note:

- One item is cropped off at the bottom of the list
- Green rows indicate delivered items
- Non-green rows indicated not currently purchased items, that are still required
- Some of the grey columns in totals table is written in VBA as seen in Appendix B

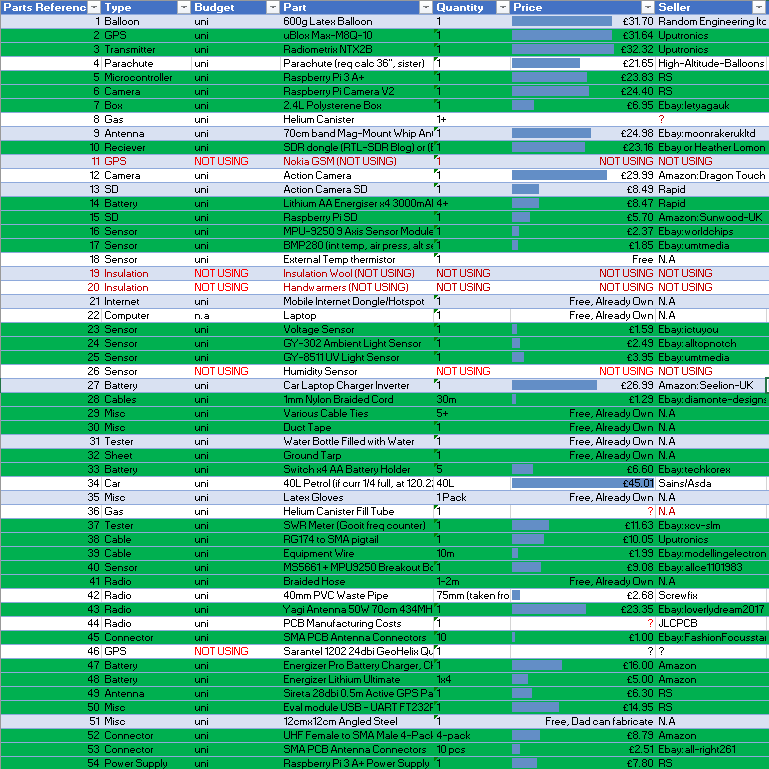
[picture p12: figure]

## 7.2 B – Excel VBA Code to Perform Totalling and Colouring Operations

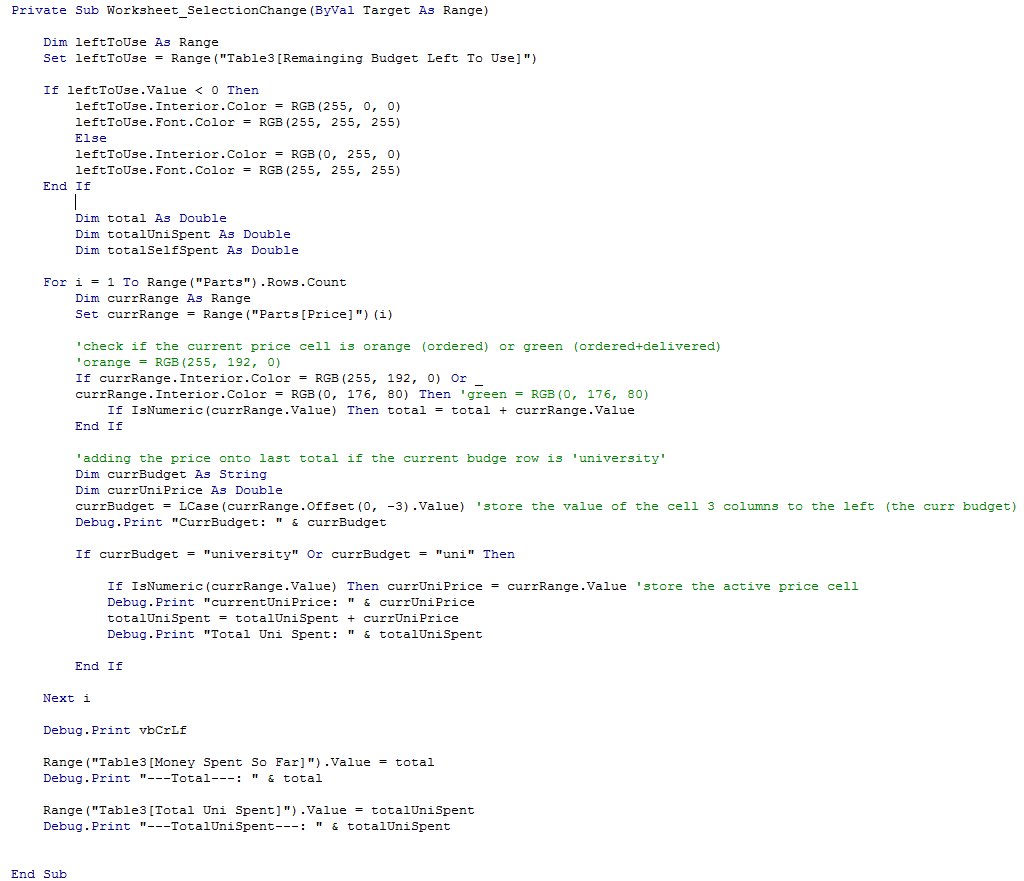
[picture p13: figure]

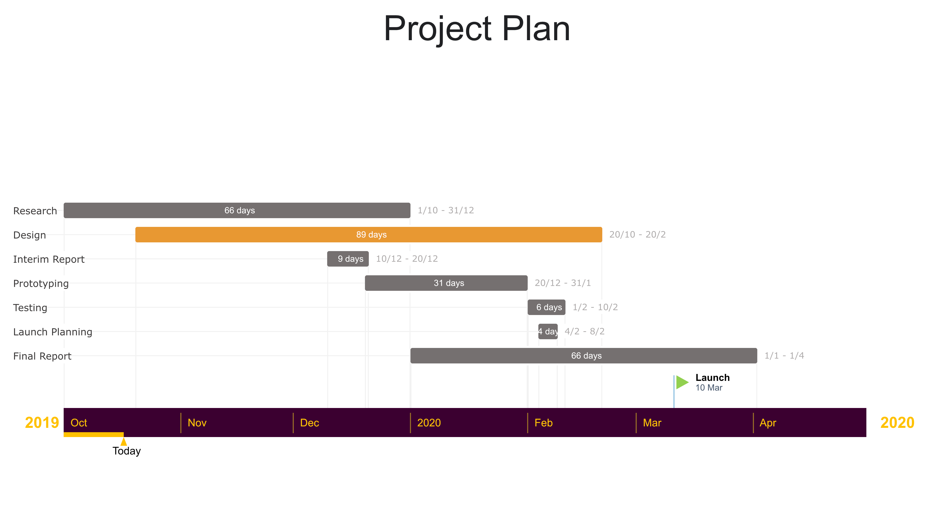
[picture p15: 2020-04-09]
Proposal/Gaant Chart.png

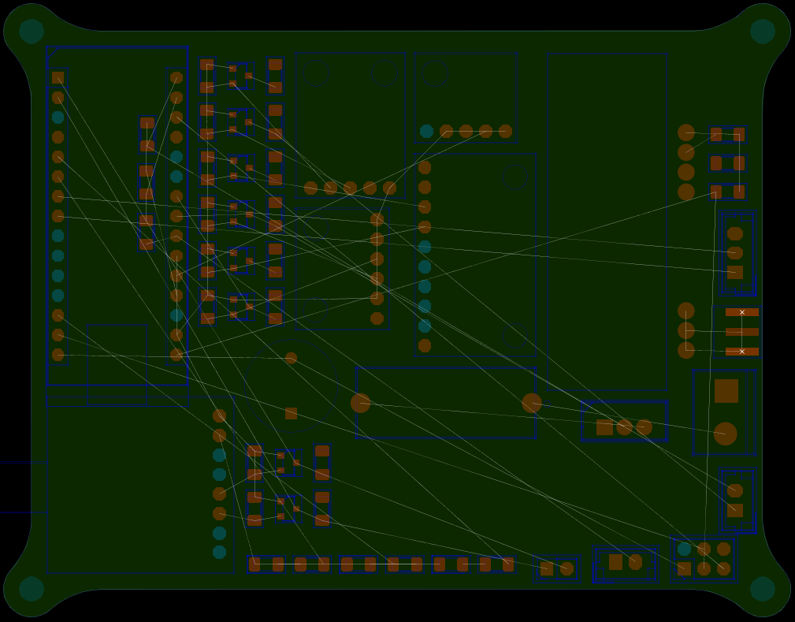
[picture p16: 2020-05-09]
Flight Tracker PCB (Nano Version)/Flight Tracker/Specctra DSN/With Zones/before autorouter.png

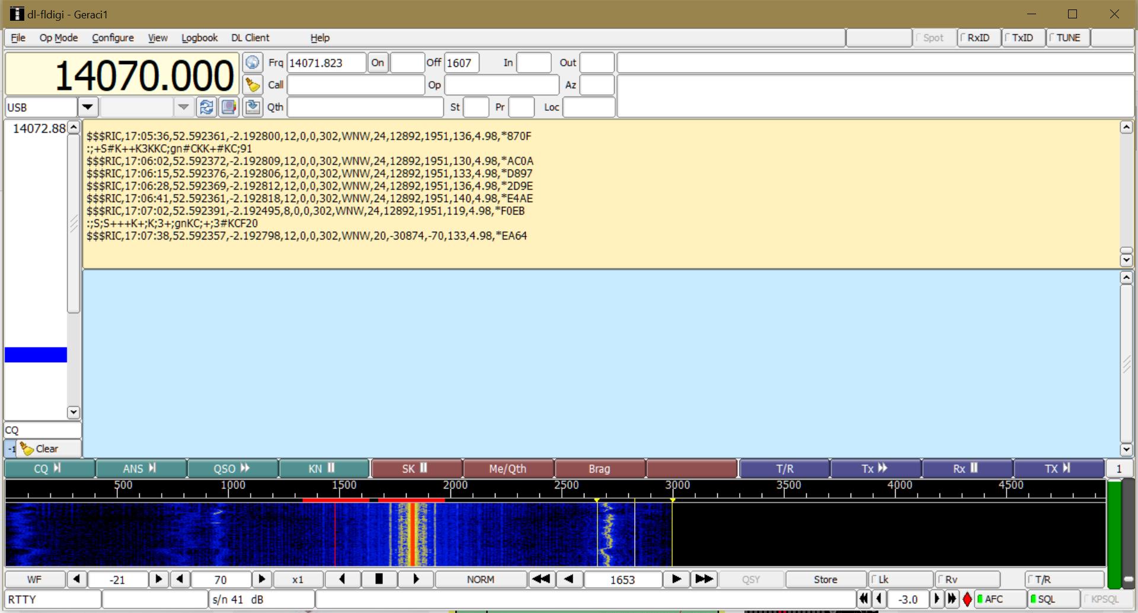
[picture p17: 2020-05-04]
Screenshot/Thesis/DL-Fldigi showing RTTY smooth RTTY tone when GPS disconnected.jpg

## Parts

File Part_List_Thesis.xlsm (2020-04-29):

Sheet: Part List
Parts Reference | Type | Budget | Part | Quantity | Price | Seller | Avail at | Comment
1 | Balloon | uni | 600g Latex Balloon | 1 | £31.70 | Random Engineering ltd | http://www.randomengineering.co.uk/Random_Aerospace/Balloons.html | Kaymont: 600g totex TA600 natural latex, helium 1-2lbs payload 250m/min 02.11.19
2 | GPS | uni | uBlox Max-M8Q-10 | 1 | £31.64 | Uputronics | https://store.uputronics.com/index.php?route=product/product&path=60_64&product_id=84 | This GPS module is proven to work beyond the altitude that the average GPS module will stop working. So there is no radio down time.
3 | Transmitter | uni | Radiometrix NTX2B | 1 | £32.32 | Uputronics | https://radiometrix.mybigcommerce.com/ntx2b-uhf-narrow-band-fm-transmitter-frequency-434-075mhz-434-650mhz-and-458-700mhz/ | The heart of the payload transmitter. Licence free due to the low output power of 10mW. Not to worry since, the sky has VERY good line of sight, but becomes a problem when the balloon payload lands, hence the requirement of a YAGI directional antenna to pick up faint signals
4 | Parachute | uni | Parachute (req calc 36", sister) | 1 | £21.65 | High-Altitude-Balloons | http://www.high-altitude-balloon.com/Payload-Parachute-Balloon-Parachute-Instrument-Chute/payload-parachute-balloon-chute-radiosonde-chute-36inch | 36 inch parachute as a safeguard at the moment, may need smaller or bigger, depends on payload weight and balloon rements after burst. May have sister fabricate one for cheaper. The price is shown is inclusive of $8 delivery, $20 without delivery
5 | Microcontroller | uni | Raspberry Pi 3 A+ | 1 | £23.83 | RS | https://uk.rs-online.com/web/p/processor-microcontroller-development-kits/1811853/ | The Raspi 3 A+ will be used as the brain of the payload, A+ means it will use less power that other versions of the pi, and hence not waste the lithium cells onboard. Though will it generate enough heat to keep everything warm?
6 | Camera | uni | Raspberry Pi Camera V2 | 1 | £24.40 | RS | https://uk.rs-online.com/web/p/video-modules/9132664/ | The Raspi V2 camera will be used to capture onboard still photos and will be trigger by using a on raspberry pi script that will trigger photos to be taken every 30s or so. This should
7 | Box | uni | 2.4L Polysterene Box | 1 | £6.95 | Ebay:letyagauk | https://www.ebay.co.uk/itm/THERMO-INSULATION-POLYSTYRENE-BOXES-FOOD-FISH-REPTILES-PERISHABLE-VARIOUS/233207982930 | A box to house the payload electronics which is lightweight, highly insulating, impact cushioning. Changed from 8L to 2.4L since steve randall said it was overally large
8 | Gas | uni | Helium Canister | 1+ | £80.00 | ? |  | I neeed to figure out how much helium I will need, but that depends on the payload total weight, and various other factors, use online helium calculator!
9 | Antenna | uni | 70cm band Mag-Mount Whip Antenna cut to 164mm | 1 | £24.98 | Ebay:moonrakerukltd | https://www.ebay.co.uk/itm/HAM-Antenna-Kit-Magnetic-Mount-Antenna-DUAL-BAND-2m-70cm/122953868791 | This is the antenna that will be connected to the SDR dongle plugged in the laptop in the chase car. The vertical element need to be 164mm 70cm band 434MHz. Single band preferrably
10 | Reciever | uni | SDR dongle (RTL-SDR Blog) or (EZCap) or NEWSKY TV28T dongle / Yaesu 817 | 1 | £23.16 | Ebay or Heather Lomond | https://www.ebay.co.uk/itm/RTL-SDR-Blog-V3-RTL2832-1PPM-TCXO-HF-BiasT-SMA-Software-Defined-Radio-Antennas/283144516411 | RTL-SDR Blog V3 RTL2832 1PPM TCXO HF BiasT SMA Software Defined Radio + Antennas
11 | GPS | NOT USING | Nokia GSM (NOT USING) | 1 | NOT USING | NOT USING | NOT USING | NOT USING
12 | Camera | uni | Action Camera | 1 | £29.99 | Amazon:Dragon Touch | amazon.co.uk/Dragon-Touch-Anti-shake-Microphone-Accessories/dp/B07W7P1Y9V/ref=sr_1_3?crid=18VO25A8JLBIZ&keywords=dragon+touch+4k+action+camera&qid=1575238316&sprefix=Dragon+Touch%2Caps%2C328&sr=8-3 | This action camera will be used to take either video footage or still photos, pointing 30 degrees down to capture the curvature of the Earth
13 | SD | uni | Action Camera SD | 1 | £8.49 | Rapid | https://www.rapidonline.com/kingston-sdcs-64gb-canvas-select-microsdxc-card-64gb-19-7990 | The SD card is required to store the capture images and videos from the action camera
14 | Battery | uni | Lithium AA Energiser x4 3000mAh =12,000mAh (1.5v*4) = 6V | 4+ | £8.47 | Rapid | https://www.rapidonline.com/energizer-639155-hi-energy-lithium-aa-battery-3000mah-x4-59-1152 | These will be required for powering the electronics on the payload, several packs will likely be needed, for testing, actual launch, externally powering the action cameras, rpi, radio tracker, all the sensors, GPS ect. Higher voltages will probably be required. This will be determined when I come to build it
15 | SD | uni | Raspberry Pi SD | 1 | £5.70 | Amazon:Sunwood-UK | https://www.amazon.co.uk/gp/product/B06XFSZGCC/ | This SD card is needed as means of storage for the raspberry pi photo/and scripts that will run on the pi. Raspberry pi website says the pi bootlooder can only read FAT filesystem, which is is 32GB or less. Changed it from 64GB micro sd because that will be a ExFAT file system!
16 | Sensor | uni | MPU-9250 9 Axis Sensor Module (3 acc, 3 gyr, 3 magno) | 1 | £2.37 | Ebay:worldchips | https://www.ebay.co.uk/itm/MPU-9250-SPI-IIC-9-Axis-Attitude-Module-Gyro-Accelerator-Magnetometer/221545416146 | This will gather data on 3 axis accelerometer, 3 axis gyroscope, and 3 axis magnometer
17 | Sensor | uni | BMP280 (int temp, air press, alt sensor) | 1 | £1.85 | Ebay:umtmedia | https://www.ebay.co.uk/itm/BMP280-3-3V-Pressure-Sensor-Module-Arduino-Precision-Atmospheric-Replace-BMP180/262945369944 | BMP180, or successor; BMP280, GY995, MPU…, Steve Randall says the BMP280 does not measure above 30,000ft since the sensor has a range of -500m to 9000m, or 300hPa to 1100hPa. The MS5561 has a range that goes down to 10hPa, but it cannot be found online as easily
18 | Sensor | uni | External Temp thermistor | 1 | Free | N.A | N.A | I can get this from the Mechatronics lab, possibily. Will be externally mounted on the payload to gather external stratosphere temperature. Likely to get peak value of -55 degrees C
19 | Insulation | NOT USING | Insulation Wool (NOT USING) | NOT USING | NOT USING | NOT USING | NOT USING | NOT USING
20 | Insulation | NOT USING | Handwarmers (NOT USING) | NOT USING | NOT USING | NOT USING | NOT USING | NOT USING
21 | Internet | uni | Mobile Internet Dongle/Hotspot | 1 | Free, Already Own | N.A | N.A | The laptop in the chase car will need to have an internet connection to relay the information to HABHUB. This can be done with internet dongle or mobile hotspot
22 | Computer | n.a | Laptop | 1 | Free, Already Own | N.A | N.A | An existing laptop will be needed in chase car to track the position of the balloon in flight with a SDR dongle or proper radio using the DL-Fldigi software, which will relay the information to HABHUB to allow others to track the balloon
23 | Sensor | uni | Voltage Sensor | 1 | £1.59 | Ebay:ictuyou | https://www.ebay.co.uk/itm/Arduino-25v-DC-Input-Voltage-Sensor-Module-Tester-Board-DC001/223529777639 | Arduino 25v DC Input Voltage Sensor Module Tester Board DC001, to test the voltage of the battery during the flight to see data later on
24 | Sensor | uni | GY-302 Ambient Light Sensor | 1 | £2.49 | Ebay:alltopnotch | https://www.ebay.co.uk/itm/GY-302-BH1750-Digital-Ambient-Light-Intensity-Sensor-Module-I2C-BH1750FVI-16bit/233344174745 | The ambient light sensor is just a sensor to gather data on the amount of light that is present during the flight, Heather used one
25 | Sensor | uni | GY-8511 UV Light Sensor | 1 | £3.95 | Ebay:umtmedia | https://www.ebay.co.uk/itm/GY-8511-ML8511-Sensor-Module-Ultraviolet-Analog-Output-UV-Sensor-for-Arduino-PI/263238052251 | The UV light sensor is to gather data on the amount of UV exposure during the flight. Likely that it will go up as the balloon rises in altitude
26 | Sensor | NOT USING | Humidity Sensor | NOT USING | NOT USING | NOT USING | NOT USING | NOT USING
27 | Battery | uni | Car Laptop Charger Inverter | 1 | £26.99 | Amazon:Seelion-UK | https://www.amazon.co.uk/Universal-Charger-Inverter-Computer-Sumsung/dp/B0792N9F5M/ | Is required for laptop in car, to keep it alive since It will be dead by time we have reached the payload
28 | Cables | uni | 1mm Nylon Braided Cord | 30m | £1.29 | Ebay:diamonte-designs | https://www.ebay.co.uk/itm/400559282398 | This will be used to connect balloon to parachute to payload, and copes with the cold well, but doesn't have a overally high UTS as stated by the regulations requirements
29 | Misc | uni | Various Cable Ties | 5+ | Free, Already Own | N.A | Already Own | Used to connect the baloon and nylon lines
30 | Misc | uni | Duct Tape | 1 | Free, Already Own | N.A | Already Own | Use to seal helium in the balloon, and payload lid on
31 | Tester | uni | Water Bottle Filled with Water | 1 | Free, Already Own | N.A | Free | Used to calculate the positive lift in helium calculator at time of launch
32 | Sheet | uni | Ground Tarp | 1 | Free, Already Own | N.A | N.A | This is important to protect the latex balloon at the launch site from the ground to prevent prematurely rupturing it. I can aquire this from my father's work (giant bin bags)
33 | Battery | uni | Switch x4 AA Battery Holder | 5 | £6.60 | Ebay:techkorex | https://www.ebay.co.uk/itm/AA-x-4-Battery-Holder-with-Connection-Wire-Cable-and-On-Off-Switch/192587484441 | I can get this sort of thing from the mechatronics lab, and do not have to purchase it, but since I want to battery to have a built in switch I have chosen to source it from Ebay.
34 | Car | uni | 40L Petrol (if curr 1/4 full, at 120.22L/pl) | 40L | £45.01 | Sains/Asda | N.A | If I purchase 3/4 of a 50L tank of petrol from sainsburys or asda. Balloon typically land 3 hours away, to a full tank is important.
35 | Misc | uni | Latex Gloves | 1 Pack | Free, Already Own | N.A | N.A | Previous guides have said it is important not to touch the balloon with bare hands because of the oils on your hand can cause prematurely bursting
36 | Gas | uni | Helium Canister Fill Tube | 1 | ? | N.A | N.A | I need to buy or fabricate a helium fill tube that will connect the helium canister to the balloon and which will transfer the helium to inflate the balloon
37 | Tester | uni | SWR Meter (Gooit freq counter) | 1 | £11.63 | Ebay:xcv-slm | https://www.ebay.co.uk/itm/GOOIT-GY560-50Mhz-to-2-4Ghz-PROTABLE-FREQUENCY-COUNTER-UK-Stock/293269783628 | Used for tuning the reciving antenna/transmitter to resonated 434MHz on the 70cm band
38 | Cable | uni | RG174 to SMA pigtail | 1 | £10.05 | Uputronics | https://store.uputronics.com/index.php?route=product/product&path=63&product_id=59 | This is required for the GPS transmitter RF connection to payload antenna
39 | Cable | uni | Equipment Wire | 10m | £1.99 | Ebay:modellingelectronics | https://www.ebay.co.uk/itm/113895625282 | Needed to great payload antenna ground plane
40 | Sensor | uni | MS5661 + MPU9250 Breakout Board | 1 | £9.08 | Ebay:allce1101983 | http://www.ebay.co.uk/itm/311518020295 | This is a superior pressure sensor, and thus altermeter than the one on the BMP280. Since the one on the BMP280 does not function beyound 100hPa (30,000ft) where as the MS5561 altermeter, works up to 100,000ft (10hPa). Although, it is very difficult to find it online. This is combined with the MPU9250 which provides the 3 axis acc, 3 axis gyro, and 3 axis magno
41 | Radio | uni | Braided Hose | 1-2m | Free, Already Own | N.A | ? | This is required to connect the helium canister valve to the balloon neck to inflate the balloon
42 | Radio | uni | 40mm PVC Waste Pipe | 75mm (taken from 3m length) | £2.68 | Screwfix | https://www.screwfix.com/p/floplast-push-fit-pipe-white-40mm-x-3m/65426 | 75mm is needed to make a fill tube for the balloon (Helium to balloon tube)
43 | Radio | uni | Yagi Antenna 50W 70cm 434MHz | 1 | £23.35 | Ebay:loverlydream2017 | https://www.ebay.co.uk/itm/Aluminum-UHF-F-7dBi-High-Gain-Yagi-Base-Station-Antenna-Adjust-For-2-Way-Radio/123888257289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 | This YAGI is likely required for when the signal is lost upon landing of the payload. Typically the poor line of sight causes signal loss. A YAGI is extreme directional and can be use to pick up faint signals and thus aid in locating the payload
44 | Radio | uni | PCB Manufacturing Costs | 1 | ? | JLCPCB | N.A | Since I need to develope a PCB in kicad, I need to have it made profressionally. I used JLCPCB in my second year for CAN bus, and they provided very nice boards
45 | Connector | uni | SMA PCB Antenna Connectors | 10 | £1.00 | Ebay:FashionFocusstar | https://www.ebay.co.uk/itm/1-10Pcs-0-062-SMA-Female-Jack-Adapter-Solder-Edge-PCB-Straight-Mount-Connector/153635255449 | Required to connect the antenna of the payload to the PCB tracker, only need one but pack of 10 is cheaper, except it is from china
46 | GPS | NOT USING | Sarantel 1202 24dbi GeoHelix Quad Antenna GPS (NOT USING) | 1 | ? | ? | ? | ?
47 | Battery | uni | Energizer Pro Battery Charger, Charges AA and AAA Batteries, (4 AA Rechargeable Batteries Included) | 1 | £16.00 | Amazon | https://www.amazon.co.uk/Energizer-Battery-Batteries-Rechargeable-Included-Black/dp/B001P8OCCS | Need rechargable battery for testing phase
48 | Battery | uni | Energizer Lithium Ultimate | 1x4 | £5.00 | Amazon | https://www.amazon.co.uk/Energizer-Ultimate-Lithium-Batteries-Pack/dp/B000IWW1G6 | These will be required for the actual flight, cannot rely on recharable batterys. These are the worlds longest lasting batteries
49 | Antenna | uni | Sireta 28dbi 0.5m Active GPS Patch Antenna | 1 | £6.30 | RS | https://uk.rs-online.com/web/p/gps-antennas/1408050/ | This is an important antenna that will be plugged into the GPS breakout board. Uputronics' Anthony confirmed this is the correct antenna for the GPS board, after the geohelix santarel antenna has been discontinued
50 | Misc | uni | Eval module USB - UART FT232RL UM232R | 1 | £14.95 | RS | https://uk.rs-online.com/web/p/interface-development-kits/0406568/ | This is required to observing serial print with PUTTY as d0 and d1 of the arduino are being used by UART. So you need an external board according to Anthony Stirk.
51 | Misc | uni | 12cmx12cm Angled Steel | 1 | Free, Dad can fabricate | N.A | N.A | This is required for the GPS patch antenna to simulate a ground plane, increases the gain by 1.5-2.5dB by doing this. Will be fixed to top of lid of payload and patch antenna will be magnetically mounted to the steel bracket
52 | Connector | uni | UHF Female to SMA Male 4-Pack | 4-pack | £8.79 | Amazon | https://www.amazon.co.uk/gp/product/B01GP9VKHQ/ | The YAGI antenna I receive has only a UHF connector, so I needed a UHF female to SMA male adapter in order to connect the antenna to the USB SDR. I purchased a 4-pack to ensure I have all the types of adapting that may come up.
53 | Connector | uni | SMA PCB Antenna Connectors | 10 pcs | £2.51 | Ebay:all-right261 | https://www.ebay.co.uk/itm/264494080517 | Had to order these, because the seller I bought the others from sent only 1 pcs for £1!! (Ebay:FashionFocusstar)
54 | Power Supply | uni | Raspberry Pi 3 A+ Power Supply | 1 | £7.80 | RS | https://uk.rs-online.com/web/p/ac-dc-adapters/9098126/?src=raspberrypi | Offical power supply by Raspberry Pi. Provides the right amount of power for a raspberry with and without usb items plugged into it 2.5A
55 | Misc | uni | Rpi GPIO reference plate | 1 | £4.00 | Amazon:Home-Ideas | https://www.amazon.co.uk/gp/product/B07RX2F2PP/ | Gives labels to the GPIO pins of the raspberry pi, since they have no labels and I don't think counting them will be fun after a while
56 | PCB | uni | 4 Channels IIC I2C Logic Level Converter Bi-Directional Module 3.3V to 5V Shifter | 1 pack of 10pcs | £5.99 | Amazon:Guangzhouxinqinwangluokeji | https://www.amazon.co.uk/gp/product/B07RDHR315/ref=ppx_yo_dt_b_asin_title_o00_s00 | Breadboard voltage level shifting only. Will implement directly on PCB in actual version
57 | PCB | uni | FQP47P06 P Channel Mosfet | 1 pack of 5 | £9.56 | RS | https://uk.rs-online.com/web/p/mosfets/6715127/ | Required for providing reverse voltage protection for the PCB supply pins to prevented destruction of the PCB
58 | PCB | uni | Trimmer Pots Mix Pack | 1 pack of 26 | £5.95 | Ebay:quartertosix_ltd | https://www.ebay.co.uk/itm/Trimmer-Potentiometer-Variable-Resistor-100R-to-1M-13-values-Single-or-Mix-Pack/153158237986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 | 100k pot required for radio pin of the NTX2B to tune the frequency shift
59 | PCB | uni | Arduino Uno Clone | 1 | £4.79 | Ebay:happybuddhatrading | https://www.ebay.co.uk/itm/Arduino-Uno-R3-compatible-ATMEGA328-CH340G-USB-UK-Stock/322898299808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 | Needed because I accidentally attempted to upload Anet A8 bootloader and now I cannot upload via USB to the arduino uno.
 |  |  | Heatsinks | 1
61 | GPS | uni | REPLACEMENT uBlox Max-M8Q-10 | 1 | £33.05 | Uputronics | https://store.uputronics.com/index.php?route=product/product&path=60_64&product_id=84 | Last one stopped working!!
Price Total | Personal Budget | University Budget | Niki Project Donation | Total Uni Budget | Remainging Budget Left To Use | Money Spent So Far | Total Uni Spent | Formula Calculated Value
£629.89 | £100.00 | £50.00 | £200.00 | £250.00 | -£279.89 | £323.39 | £716.81 | User Typed value
 |  |  |  |  |  |  |  | Over budget!
 |  |  |  |  |  |  |  | Within Budget

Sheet: Misc Parts
Parts Reference | Type | Budget | Part | Quantity | Price | Seller | Avail at | Comment
1 | Electronics | Riccardo | x3 830 Point Breadboard | 1 | £8.99 | Amazon:ELEGOO Offical | https://www.amazon.co.uk/ELEGOO-Breadboard-Solderless-Distribution-Connecting/dp/B01M0QJTI5 | 3x 380 hole bread boards, 3 for testing multiple circuits without having to dissamble each time
2 | Electronics | Riccardo | 5 in 1 RAB Holder Breadboard ABS Base | 1 | £7.99 | Amazon:SUNFOUNDER | https://www.amazon.co.uk/SunFounder-Holder-Raspberry-Breadboard-Arduino/dp/B01LYZOPR0 | This conviently holds the breadboard and microctroller on a fixed plane. A life saver when dealing with electronics
3 | Lens | Riccardo | Magnifier Magnifying 20X Eye Glass Loupe | 1 | £5.28 | Ebay:vaki7064 | http://www.ebay.co.uk/itm/401977457350 | To help with soldering SMD components
4 | Lens | Riccardo | Loupes | 1 pack of 2 |  | Amazon
5 | Soldering Iron | Riccardo | Copper Rod Bar for Soldering Iron | 1 rod | £2.99 | Ebay:themultimetalshop | https://www.ebay.co.uk/itm/CHEAP-Copper-Round-Bar-Rod-5mm-60mm-Diameter-Various-Lengths-Available/113587766730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
Price Total | Key
£25.25 | Ordered
 | Ordered & Delivered

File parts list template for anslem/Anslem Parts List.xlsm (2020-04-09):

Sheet: Part List
Parts Reference | Type | Budget | Part | Quantity | Price | Seller | Avail at | Comment
1 | Balloon | University | 600g Latex Balloon | 1 | £31.70 | Random Engineering ltd | http://www.randomengineering.co.uk/Random_Aerospace/Balloons.html | Kaymont: 600g totex TA600 natural latex, helium 1-2lbs payload 250m/min 02.11.19
2 | Radio | University | uBlox Max-M8Q-10 | 1 | £26.39 | Uputronics | https://store.uputronics.com/index.php?route=product/product&path=60_64&product_id=84 | This GPS module is proven to work beyond the altitude that the average GPS module will stop working. So there is no radio down time.
3 | Radio | University | Radiometrix NTX2B | 1 | £21.00 | Radiometrix | https://radiometrix.mybigcommerce.com/ntx2b-uhf-narrow-band-fm-transmitter-frequency-434-075mhz-434-650mhz-and-458-700mhz/
Price Total | Personal Budget | University Budget | Niki Project Donation | Total Uni Budget | Remainging Budget Left To Use |  | Calculated Value
£79.09 | £100.00 | £50.00 | £100.00 | £150.00 | £170.91 |  | Typed value

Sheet: Misc Parts
Parts Reference | Type | Budget | Part | Quantity | Price | Seller | Avail at | Comment
1 | Electronics | Riccardo | x3 830 Point Breadboard | 1 | £8.99 | Amazon:ELEGOO Offical | https://www.amazon.co.uk/ELEGOO-Breadboard-Solderless-Distribution-Connecting/dp/B01M0QJTI5 | 3x 380 hole bread boards, 3 for testing multiple circuits without having to dissamble each time
2 | Electronics | Riccardo | 5 in 1 RAB Holder Breadboard ABS Base | 1 | £5.83 | Ebay:zysysy2012 | https://www.ebay.co.uk/itm/5-in-1-RAB-Holder-Breadboard-ABS-Base-For-Raspberry-Pi-Arduino-UNO-R3-Mega-GB/303372417361 | This conviently holds the breadboard and microctroller on a fixed plane. A life saver when dealing with electronics
Price Total
£14.82

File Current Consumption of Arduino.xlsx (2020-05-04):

Pin | Pin Max Allowable Consumption | Component | Voltage (V) | Current Consumption (mA) | Current Total (mA)
Arduino 5V Pin | 400mA USB or 900mA External if VIN=7V | Radiometrix NTX2B | 5V | 17.6 | 123.5
Arduino 3.3V Pin | 150mA (dependant on 5V current) | Ublox M8Q | 3.3V | 40 | 123.5
D12 | 35mA | Buzzer | 5V | 19 | 123.5
D2 | 35mA | WARN_LED | GPIO 5V | 16.5 | 123.5
D3 | 35mA | OK_LED | GPIO 5V | 15.2 | 123.5
D10 | 35mA | GPS_LOCK_LED | GPIO 5V | 15.2 | 123.5
 |  |  |  |  | 123.5
- | - | Arduino UNO | - | 22.6mA (no LEDs expt ON_LED) -> 48mA (L led blink on) | 123.5
 |  |  |  |  | 123.5
 | [MEASURED] Total current through 3V3 pin = 39mA (OK) |  |  |  | 123.5
 | [MEASURED] Total current through 5V pin = 17.5mA (OK) |  |  |  | 123.5
 | [MEASURED] Total current through USB VCC = 110mA (AVERAGE, OK) |  |  |  | 123.5
 |  |  |  |  | 123.5
 |  |  |  |  | 123.5
 |  |  |  |  | 123.5

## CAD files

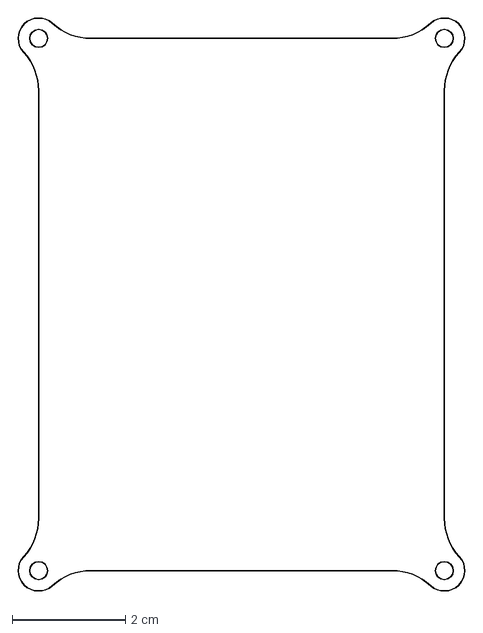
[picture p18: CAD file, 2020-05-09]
Flight Tracker PCB (Nano Version)/Flight Tracker/Arduino Uno Outline/PCB Edgecuts v1.dxf
7.95 x 10.2 cm

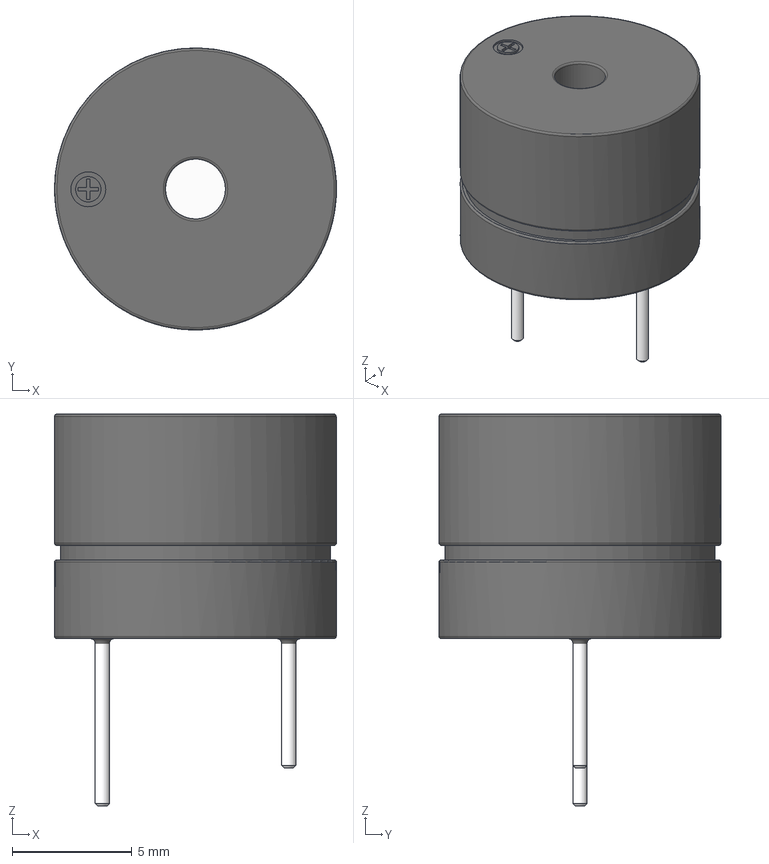
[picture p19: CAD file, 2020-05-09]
Flight Tracker PCB (Nano Version)/Models/5V Buzzer/5V Buzzer.step
11.8 x 11.8 x 16.4 mm

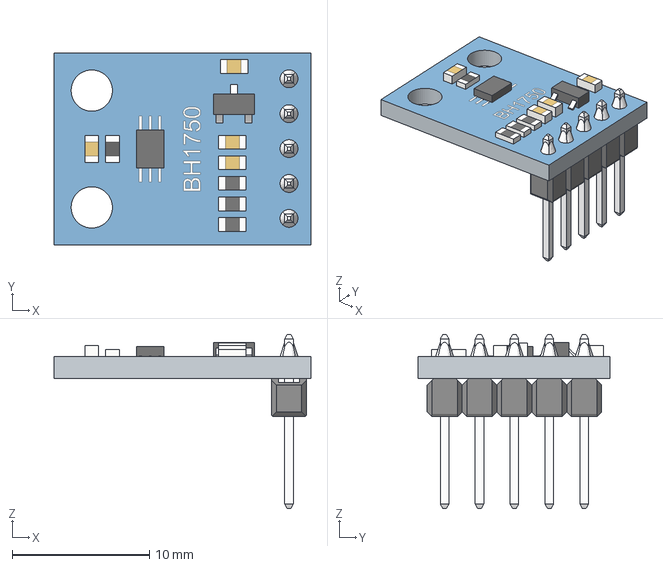
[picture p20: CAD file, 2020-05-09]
Flight Tracker PCB (Nano Version)/Models/BH1750/BH1750_Improved.step
18.7 x 14.0 x 12.7 mm

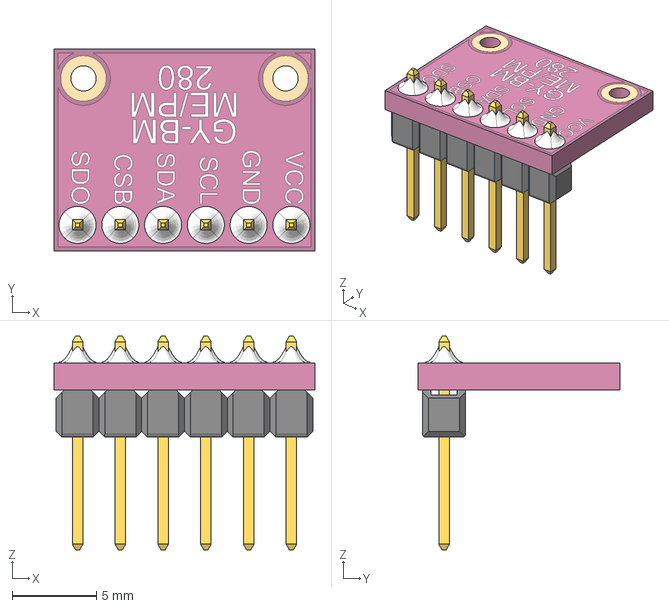
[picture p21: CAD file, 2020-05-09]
Flight Tracker PCB (Nano Version)/Models/BMP280/BMP280.step
15.5 x 12.0 x 12.7 mm

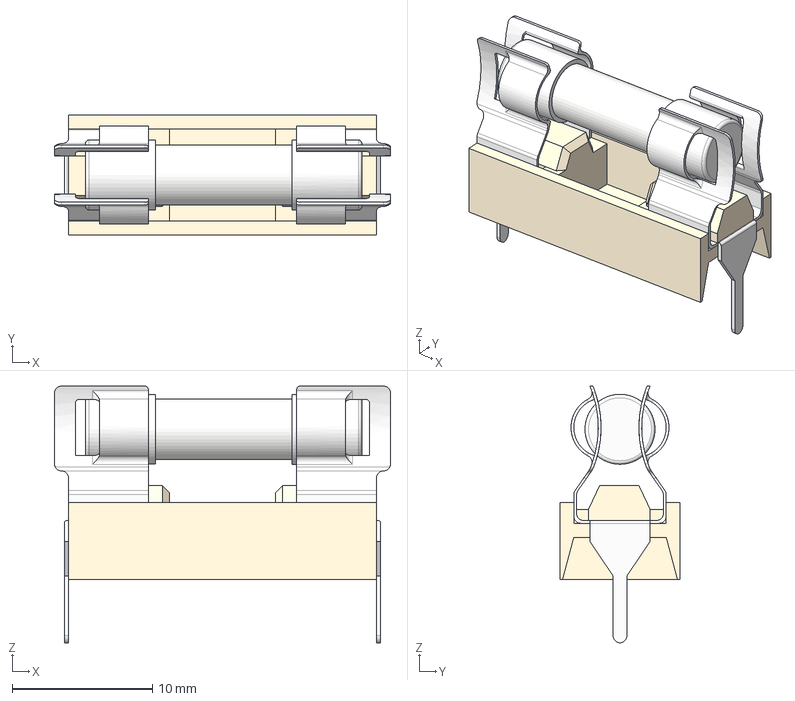
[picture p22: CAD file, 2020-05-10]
Flight Tracker PCB (Nano Version)/Models/Fuse Holder/Fuse Holder_w_Fuse.step
24.0 x 8.60 x 18.3 mm

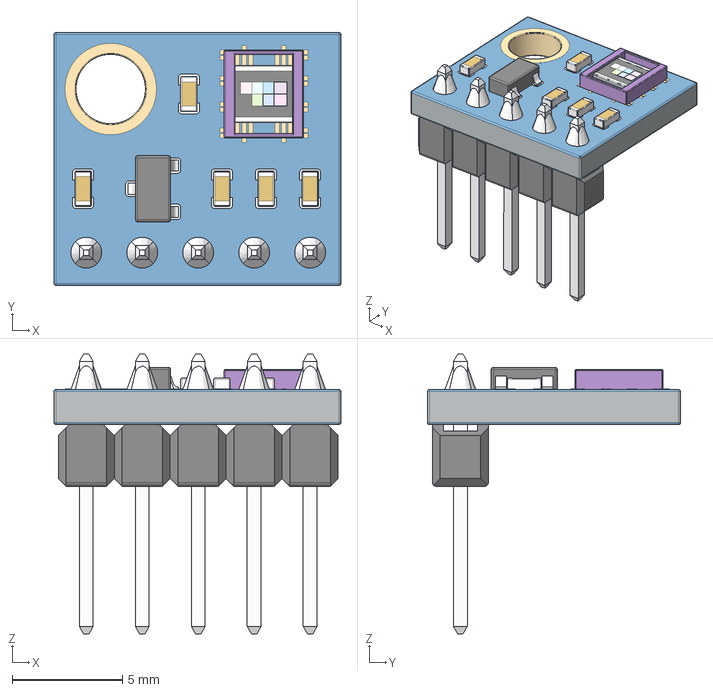
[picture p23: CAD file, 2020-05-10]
Flight Tracker PCB (Nano Version)/Models/ML8511/ML8511.step
13.0 x 11.5 x 12.7 mm
Pin Header 1x5 TH Pitch 2.54mm v1
Cap x 5

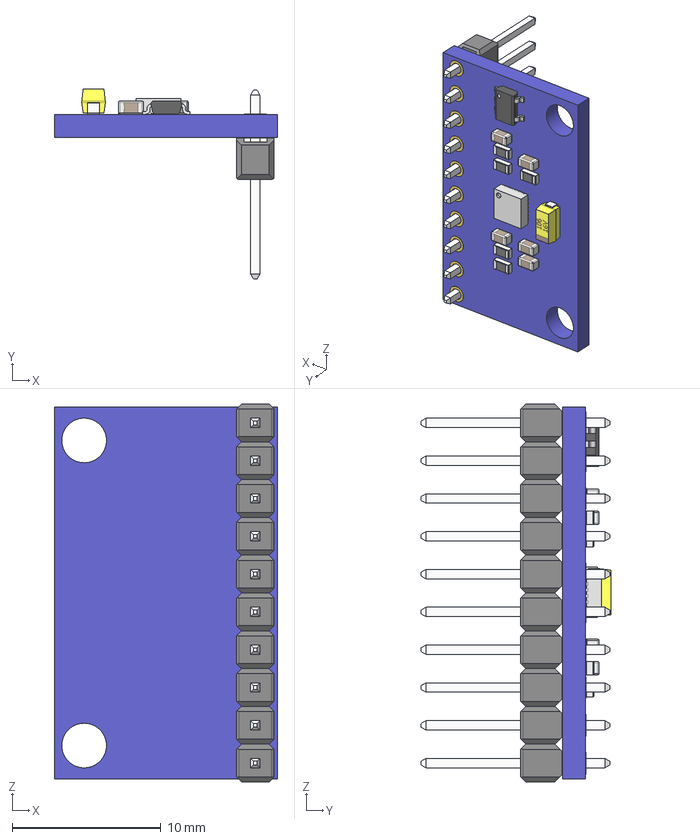
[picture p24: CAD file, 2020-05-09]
Flight Tracker PCB (Nano Version)/Models/MPU-9250/MPU-9250/MPU-9250.stp
15.0 x 12.8 x 25.4 mm
board
hole_plating x 20
Pin Header 1x10 TH Pitch 2.54mm
MPU-9250_1
tantalum 10uF
SOT23_5
RESC-0603 x 5
CAPC-0603-T0.9-BN x 5

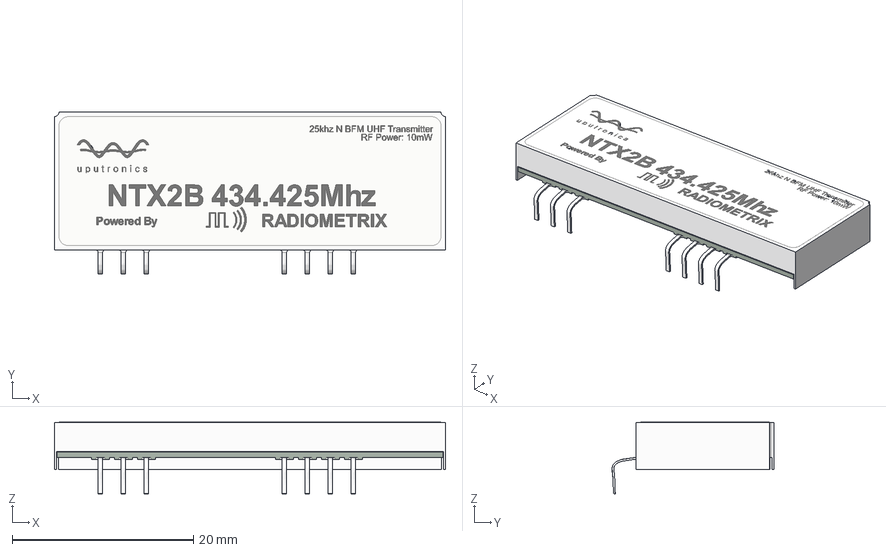
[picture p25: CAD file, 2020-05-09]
Flight Tracker PCB (Nano Version)/Models/NTX2B/NTX2B.step
43.2 x 17.9 x 7.92 mm

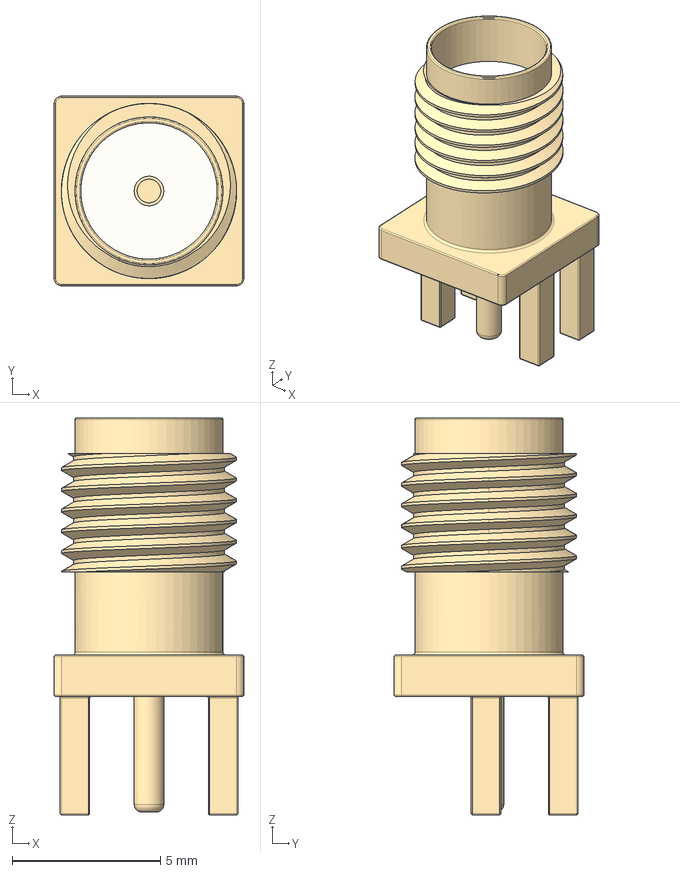
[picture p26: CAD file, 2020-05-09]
Flight Tracker PCB (Nano Version)/Models/SMA/Edge_Mounted_SMA.step
6.40 x 6.40 x 13.4 mm

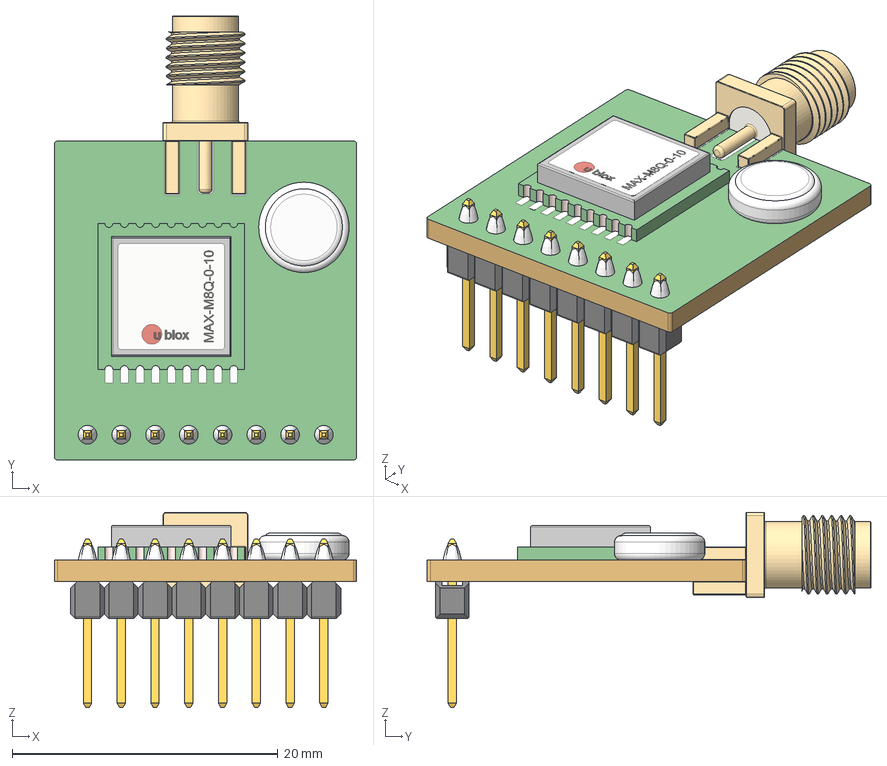
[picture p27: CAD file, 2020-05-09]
Flight Tracker PCB (Nano Version)/Models/ubloxm8q/ubloxm8q.step
22.8 x 33.4 x 14.7 mm
Pin Header 1x8 TH Pitch 2.54mm
Ublox M8Q Chip
Edge Mouted SMA

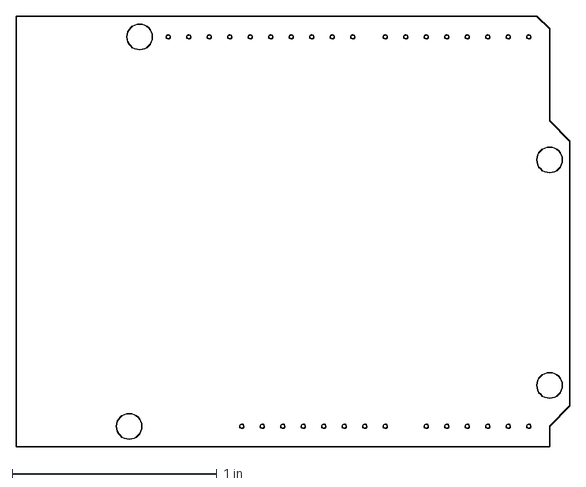
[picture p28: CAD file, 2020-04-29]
Flight Tracker PCB (Nano Version)/Flight Tracker/Arduino Uno Outline/Arduino Uno Board Outline.dxf
2.70 x 2.10 in

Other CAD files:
Flight Tracker PCB (Nano Version)/Models/MPU-9250/MPU-9250/MPU-9250_Improved.step
Flight Tracker PCB (Nano Version)/Models/NTX2B/NTX2B_Darker.step
Flight Tracker PCB (Nano Version)/Models/MPU-9250/MPU-9250/MPU-9250_Improved by Ric.step
Flight Tracker PCB (Nano Version)/Models/MPU-9250/MPU-9250/MPU-9250.iam
Flight Tracker PCB (Nano Version)/Models/MPU-9250/MPU-9250/MPU-9250_Shrinkwrap.ipt
Flight Tracker PCB (Nano Version)/Models/MPU-9250/MPU-9250/parts/CAPC-0603-T0.9-BN.ipt
Flight Tracker PCB (Nano Version)/Models/MPU-9250/MPU-9250/parts/Pin Header 1x10 TH Pitch 2.54mm.ipt
Flight Tracker PCB (Nano Version)/Models/MPU-9250/MPU-9250/parts/QFN-24 3x3 0.4mm.ipt
Flight Tracker PCB (Nano Version)/Models/MPU-9250/MPU-9250/parts/RESC-0603.ipt
Flight Tracker PCB (Nano Version)/Models/MPU-9250/MPU-9250/parts/SOT23_5.ipt
Flight Tracker PCB (Nano Version)/Models/MPU-9250/MPU-9250/parts/board.ipt
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

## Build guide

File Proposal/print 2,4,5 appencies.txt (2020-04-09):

- grayham needs to signing
- need to print appendicies 2,4 and 5
- fill the forms, scan them and upload them to canvas as one document
- Supervisor needs to sign it

page 27,28 (appendix 2)

page 30, 31, 32, 33 (appendix 4)

page 34 (appendix 5)

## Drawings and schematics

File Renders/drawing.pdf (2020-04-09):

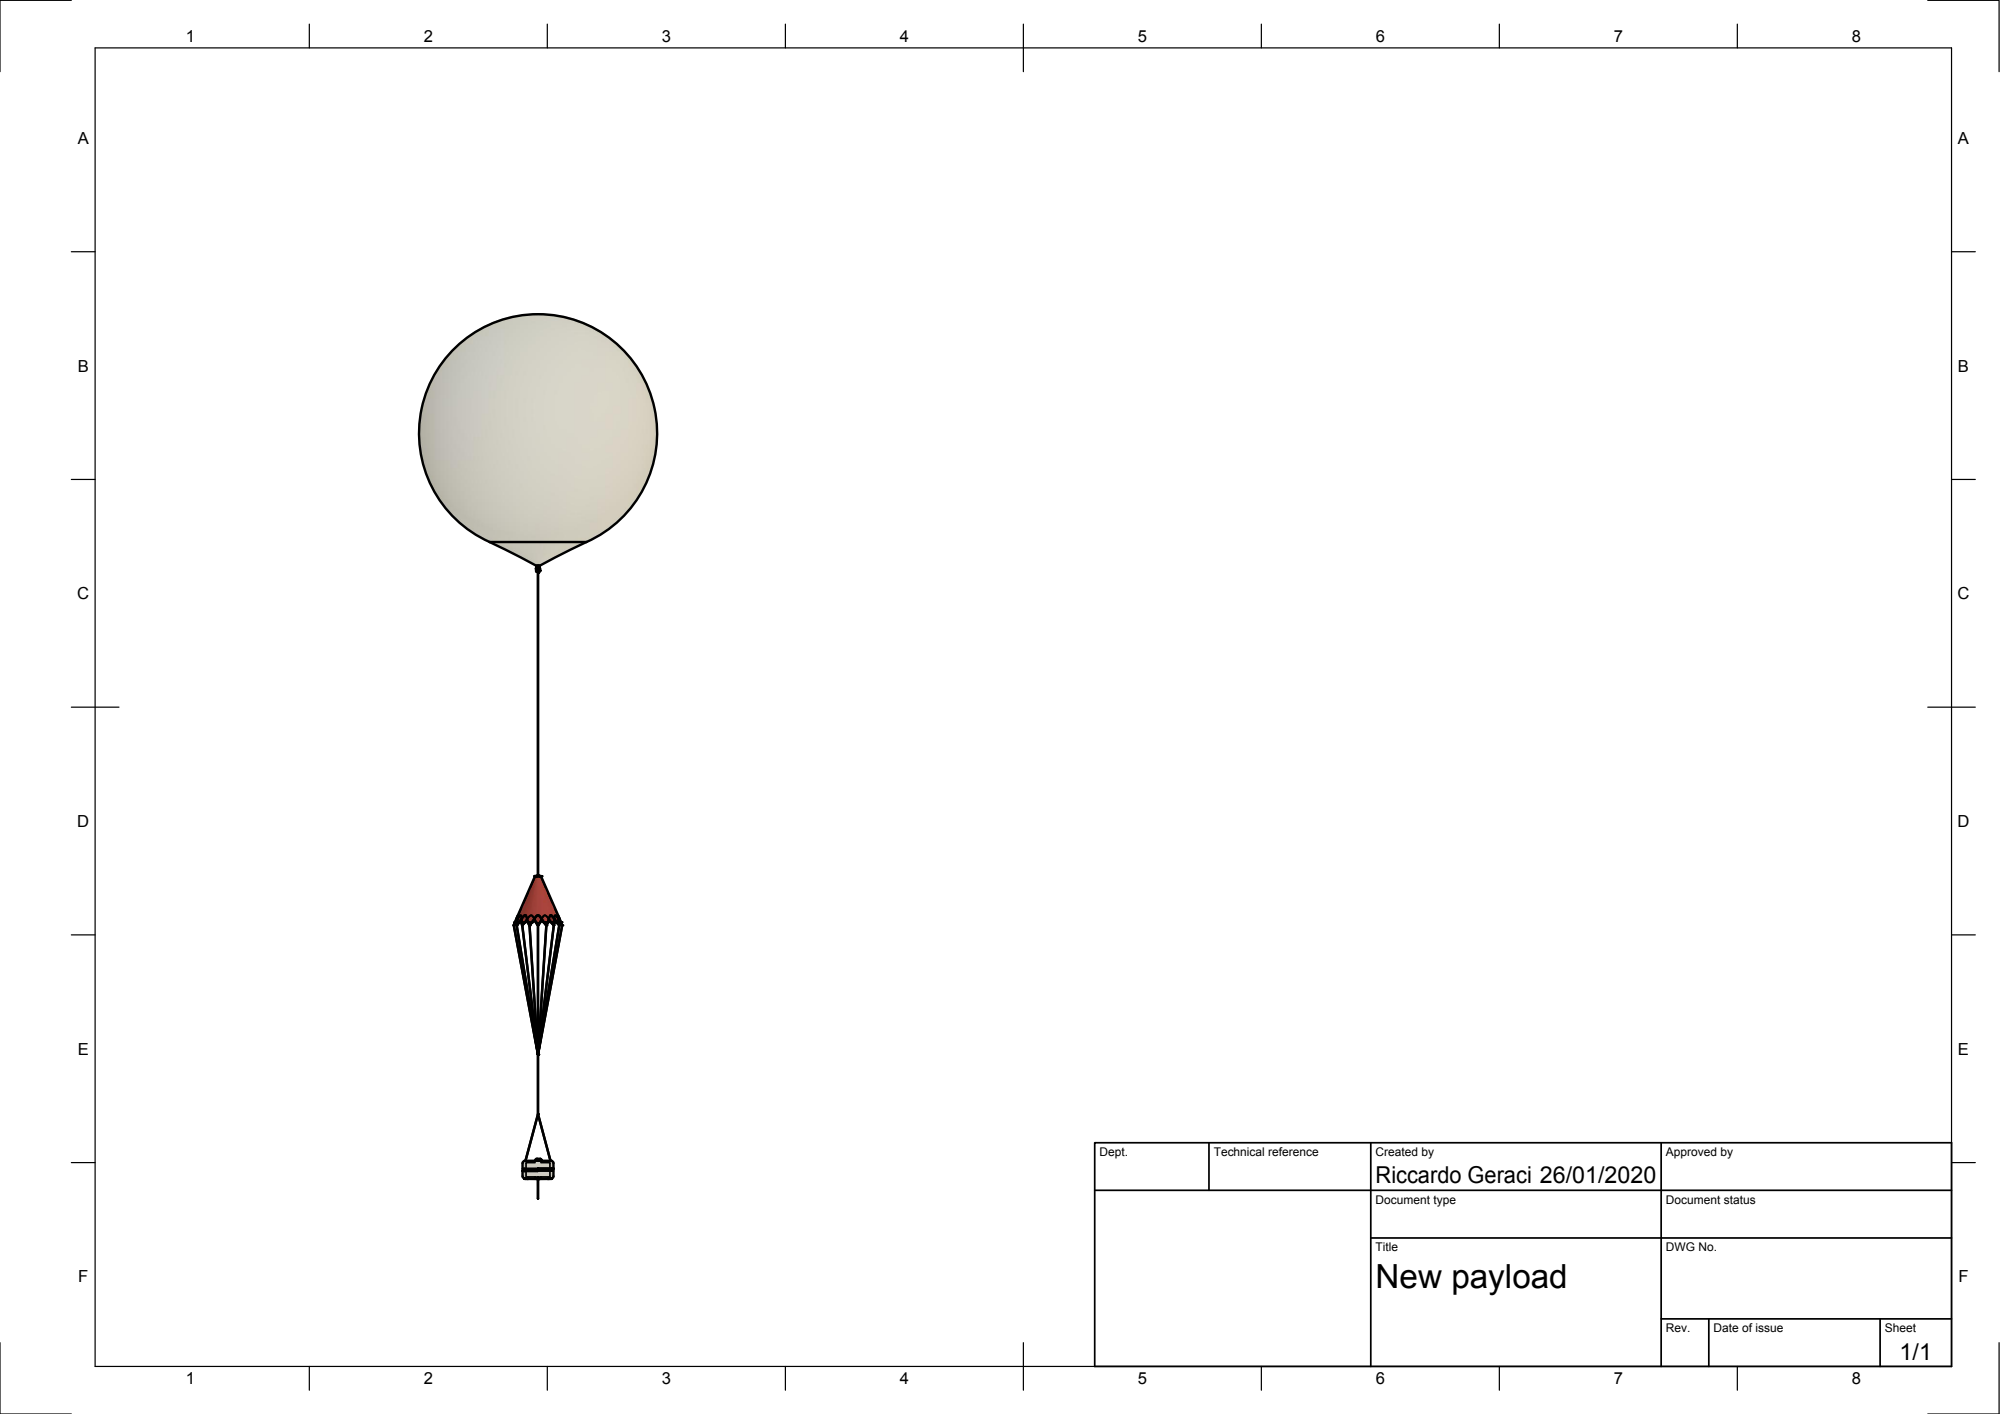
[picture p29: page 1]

Dept. | Technical reference | Created by Riccardo Geraci 26/01/2020 | Approved by

Document type | Document status

Title New payload | DWG No.

Rev. | Date of issue | Sheet 1/1

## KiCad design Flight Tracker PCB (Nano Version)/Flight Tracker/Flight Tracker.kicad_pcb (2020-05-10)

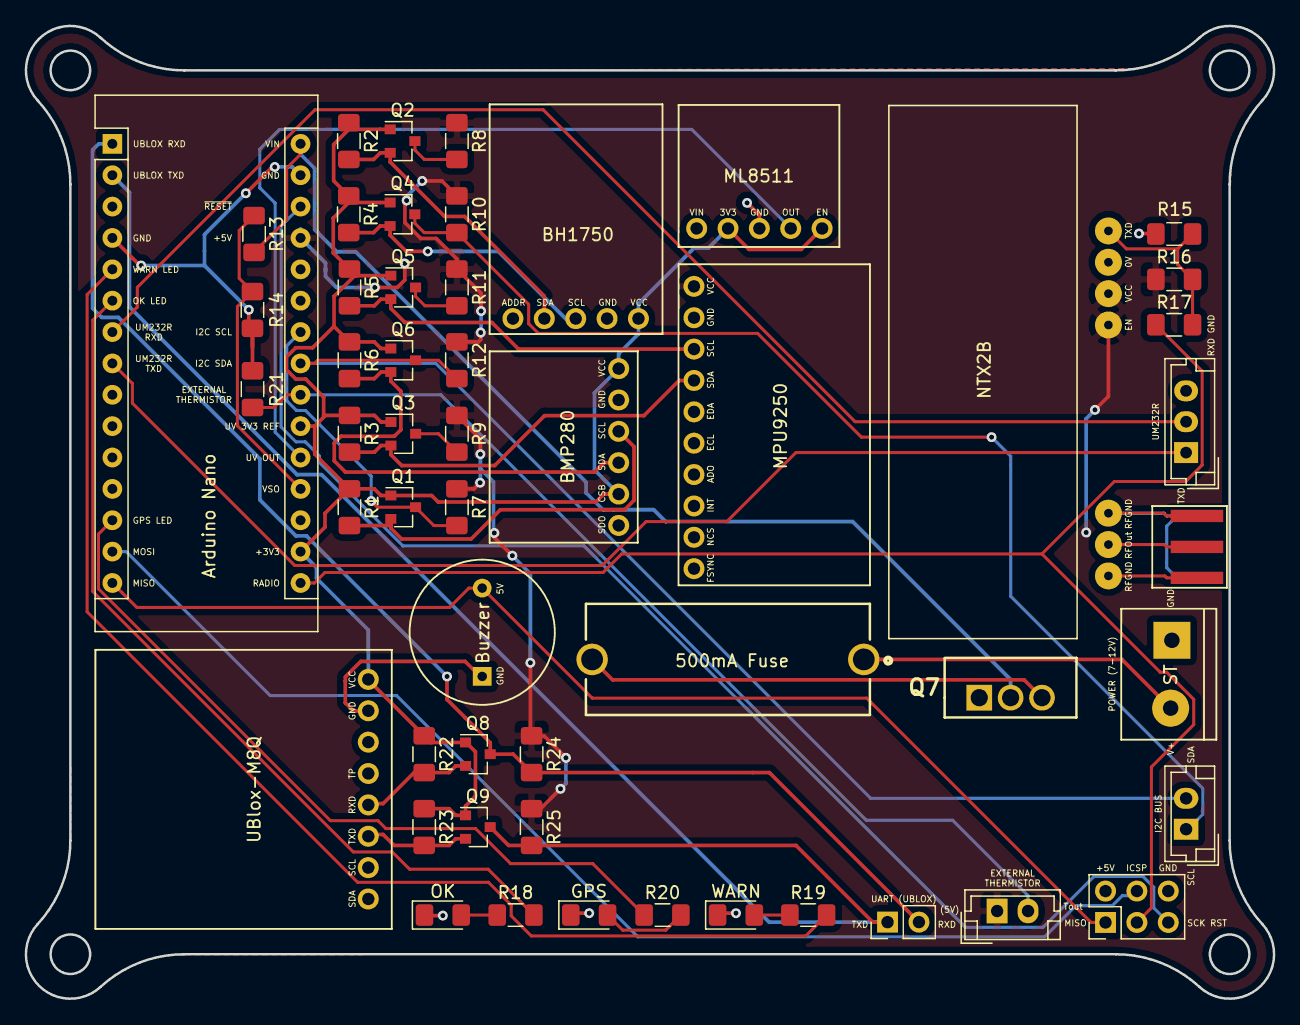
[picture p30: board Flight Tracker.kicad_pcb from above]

Board: 2 copper layers, 101.1 x 78.8 mm, 53 parts (0 on the bottom side), 40 nets.

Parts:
A1: Arduino_Nano_v3.x; Arduino_Nano_With_Model_Sockets
BZ1: Buzzer; 5V_Buzzer
D1: OK_LED; LED_1206_3216Metric_Pad1.42x1.75mm_HandSolder
D2: GPS_LOCK; LED_1206_3216Metric_Pad1.42x1.75mm_HandSolder
D3: WARN_LED; LED_1206_3216Metric_Pad1.42x1.75mm_HandSolder
F1: 500mA Fuse; MC000827_With_Model
J1, J4: Conn_01x02; JST_EH_B02B-EH-A_1x02_P2.50mm_Vertical
J2: Conn_01x02; PinHeader_1x02_P2.54mm_Vertical
J3: Screw_Terminal_01x02; 2_Pin_Screw_Terminal
J5: Conn_01x03; JST_EH_B03B-EH-A_1x03_P2.50mm_Vertical
J6: Conn_02x03_Odd_Even; PinHeader_2x03_P2.54mm_Vertical
Q1, Q2, Q3, Q4, Q5, Q6, Q8, Q9: BSS138; SOT-23
Q7: FQP47P06; TO254P483X1016X2261-3P
R1, R2, R3, R4, R5, R6, R7, R8, R9, R10, R11, R12, R22, R23, R24, R25: 10K; R_1206_3216Metric_Pad1.42x1.75mm_HandSolder
R13: 30K; R_1206_3216Metric_Pad1.42x1.75mm_HandSolder
R14: 7.5K; R_1206_3216Metric_Pad1.42x1.75mm_HandSolder
R15, R16: 4K7; R_1206_3216Metric_Pad1.42x1.75mm_HandSolder
R17: 47k; R_1206_3216Metric_Pad1.42x1.75mm_HandSolder
R18, R19, R20: 150R; R_1206_3216Metric_Pad1.42x1.75mm_HandSolder
R21: 100k; R_1206_3216Metric_Pad1.42x1.75mm_HandSolder
U1: ML8511_With_Model
U2: BH1750_With_Model
U3: SMA_5pin; SMA_EDGE
U4: NTX2_With_Model
U5: BMP280_With_Model
U6: MPU_9250_With_Model
U7: UBlox_MAX8; ublox_M8Q_with_Model

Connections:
3V3: A1.17, A1.21, Q1.1, Q2.1, Q3.1, Q4.1, Q5.1, Q6.1, Q8.1, Q9.1, R1.1, R2.1, R3.1, R4.1, R5.1, R6.1, R22.1, R23.1, U1.2, U1.5, U2.1, U5.1, U5.5, U7.8
5V: A1.27, J4.1, R7.1, R8.1, R9.1, R10.1, R11.1, R12.1, R16.1, R24.1, R25.1, U4.4, U4.5, U6.1
/I2C_SCL: A1.24, Q1.3, R7.2
/I2C_SDA: A1.23, J1.2, Q6.3, R12.2
/MISO: A1.15, BZ1.1, J6.1
/MOSI: A1.14, J6.4
/RST: A1.28, J6.5
/SCK: A1.16, J6.3, R17.1
/Thermistor: A1.22, J4.2, R21.1
/UM232R_RXD: A1.7, J5.2
/UM232R_TXD: A1.8, J5.1
/UV_OUT: A1.20, U1.4
/V_S_I: A1.30, Q7.2, R13.2
/V_S_O: A1.19, R13.1, R14.1
BH1750_SCL_3V3: Q4.2, R4.2, U2.3
BH1750_SDA_3V3: Q2.2, R2.2, U2.4
BMP280_SCL_3V3: Q1.2, R1.2, U5.3
BMP280_SDA_3V3: Q6.2, R6.2, U5.4
GND: A1.4, A1.29, BZ1.2, D1.1, D2.1, D3.1, J3.2, J5.3, J6.6, Q7.1, R14.2, R15.2, R21.2, U1.3, U2.2, U2.5, U4.6, U5.2, U5.6, U6.2, U6.10, U7.7
MPU9250_SCL_3V3: Q5.2, R5.2, U6.3
MPU9250_SDA_3V3: Q3.2, R3.2, U6.4
unnamed: A1.5, R19.2
unnamed: A1.6, R18.2
unnamed: A1.13, R20.1
unnamed: D1.2, R18.1
unnamed: D2.2, R20.2
unnamed: D3.2, R19.1
unnamed: F1.1, J3.1
unnamed: F1.2, Q7.3
unnamed: J1.1, Q4.3, R10.2
unnamed: Q2.3, R8.2
unnamed: Q3.3, R9.2
unnamed: Q5.3, R11.2
unnamed: R15.1, R16.2, R17.2, U4.7
unnamed: U3.1, U4.2
unnamed: U3.2, U4.1, U4.3
Ublox_RXD_3V3: Q8.2, R22.2, U7.4
Ublox_RXD_5V: A1.1, J2.2, Q8.3, R24.2
Ublox_TXD_3V3: Q9.2, R23.2, U7.3
Ublox_TXD_5V: A1.2, J2.1, Q9.3, R25.2

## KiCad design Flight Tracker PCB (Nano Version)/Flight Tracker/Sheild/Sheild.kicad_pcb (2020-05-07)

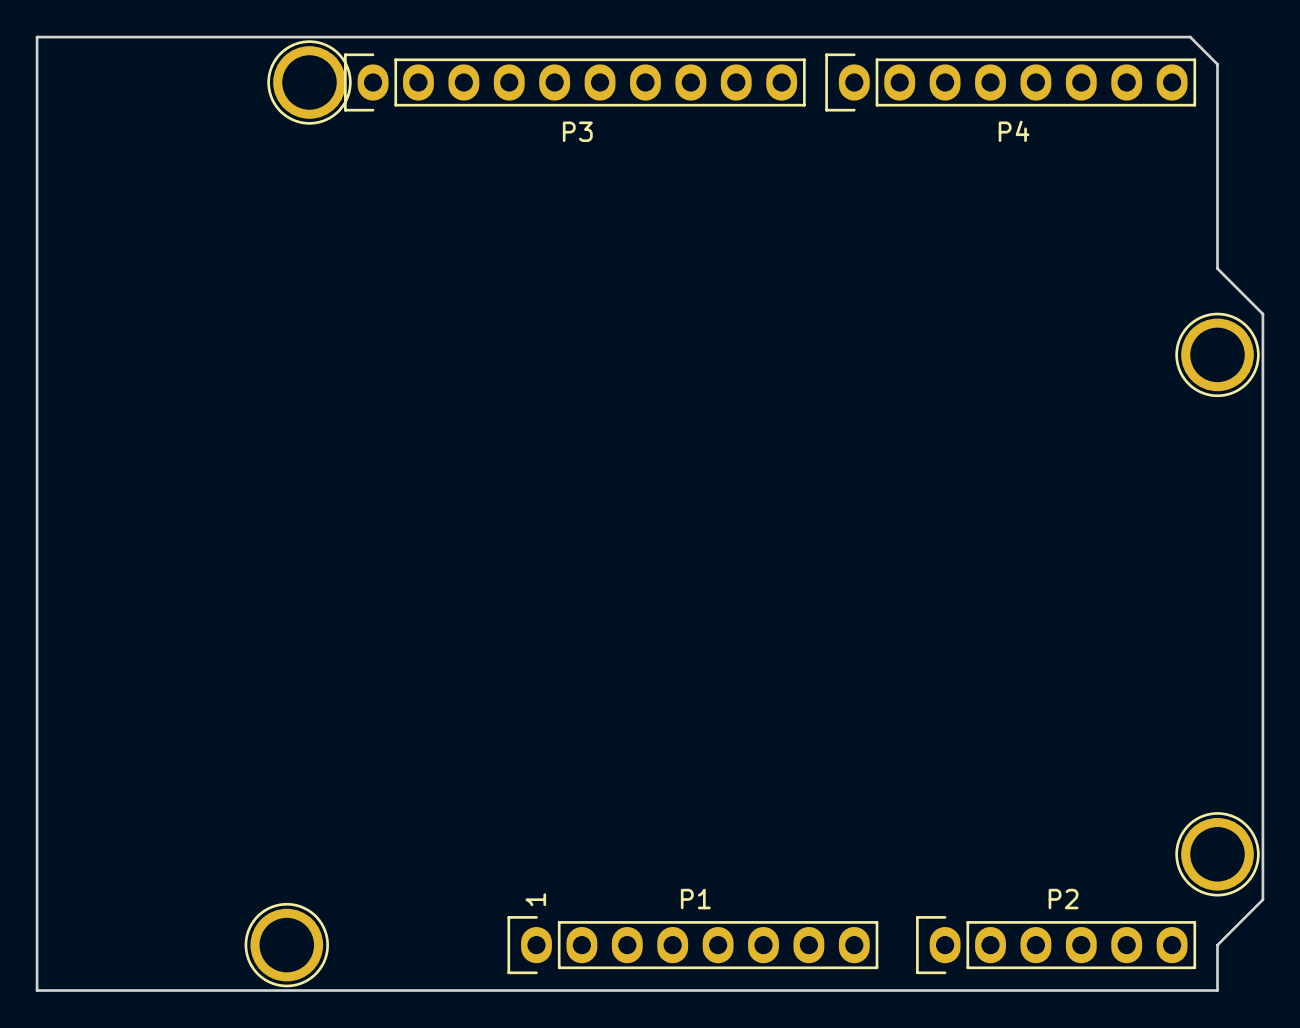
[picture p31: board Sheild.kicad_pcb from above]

Board: 2 copper layers, 68.6 x 53.3 mm, 8 parts (0 on the bottom side), 3 nets, no tracks yet.

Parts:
P1: Power; Socket_Strip_Arduino_1x08
P2: Analog; Socket_Strip_Arduino_1x06
P3: Digital; Socket_Strip_Arduino_1x10
P4: Digital; Socket_Strip_Arduino_1x08
P5, P6, P7, P8: CONN_01X01; Arduino_1pin

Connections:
/A4(SDA): P2.5, P3.2
/A5(SCL): P2.6, P3.1
GND: P1.6, P1.7, P3.4

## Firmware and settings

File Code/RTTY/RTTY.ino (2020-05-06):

#include <SoftwareSerial.h> //for debugging only
#include <string.h>
#include <util/crc16.h>
#include <TinyGPS++.h>
#include <util/delay.h>
#include <Wire.h> //needed for sensors
#include <Adafruit_Sensor.h> //adafruit unified sensor lib
#include <Adafruit_BMP280.h> //bmp280 lib
#include <BH1750.h> //light sensor lib
#include <EEPROM.h>

//RTTY @ 370Hz shift
const uint16_t RTTY_BAUD = 50; //change this to either 50 or 300 [[[rem dlfldigi too]]]
const uint8_t RTTY_ASCII = 7; //change this to either 7 or 8 [[[rem dlfldigi too]]]
const uint8_t START_BITS = 1; //[[[rem dlfldigi too]]]
const uint8_t STOP_BITS = 2; //[[[rem dlfldigi too]]]

//instances
SoftwareSerial  mySerial(5, 4); // RX/DB0, TX/DB1 for debugging only
TinyGPSPlus     gps;
Adafruit_BMP280 BMP280;
BH1750          lightmeter(0x23); //default pin->GND address

//PINS
#define RADIO_PIN 13
#define BUZZER_PIN 12
#define OK_LED 3
#define WARN_LED 2
#define GPS_LOCK_LED 10
#define BMP280_I2C_Address 0x76
#define BMP280_Altitude_Pressure_Ref 993.612 //home pressure
#define BATT_VOLTS_PIN A0
#define UVOUT_PIN A1 //uv sensor input
#define UVOUT_REF_PIN A2 //3V3 Reference pin

#define ARDUINO_RESET_PIN 11 //supply 0v/GND to reset arduino

const int16_t TIME_BETWEEN_TX = 10000; //encode and send RTTY sentence every 10secs
unsigned long RTTY_TX_Prev_Time = 0; //
const int16_t NO_GPS_Data_Reset_Thresh = 100; //RESET ARDUINO IF GPS DATA AFTER 100 ATTEMPTS

//#define DEBUG; //comment out to prevent complimate of debug lines

unsigned int GPS_Satellites;
unsigned int GPS_Hour;
unsigned int GPS_Minute;
unsigned int GPS_Second;
unsigned int GPS_Date;
double       GPS_Altitude;
double       GPS_Speed;
double       GPS_Course;
double       GPS_Latitude;
double       GPS_Longitude;
boolean      GPS_Data_Available;
uint8_t      No_GPS_Available_Count = 0;

double GPS_Distance_To_Home_In_Miles;
double GPS_Course_To_Launch_Location;
char*  GPS_Cardinial;

//Type in the launch location's GPS coords
const double LAUNCH_LOCATION_LAT = 52.682439; //Telford campus field
const double LAUNCH_LOCATION_LGN = -2.424624; //Telford campus field

//Type in your home location's GPS coords
const double HOME_LOCATION_LAT = 52.592296;
const double HOME_LOCATION_LGN = -2.192684;

//bmp280
float BMP280_Temp;
float BMP280_Pressure;
float BMP280_Altitude;

//BH1750
float BH1750_Lux;

//Voltage Sensor
double        Batt_Voltage; //query this var for voltage
int           Batt_Offset = 0; //correction offset if needed
const float   Batt_Fully_Charged_Voltage = 5.0;
uint16_t      Batt_Bleep_Start_Delay = 5000; //start delay because readings are only taken when gps data is updated
unsigned long Batt_Bleep_Prev = 0;
uint8_t       Batt_Low_Thresh = 50; //50%

//UV Sensor
float UV_Out_Voltage; //query this variable
float UV_Out_Intensity; //query this variable

//================================Aux Settings===============================================

uint8_t bBuzzRtty = 0; //beep pcb buzzer in sequence with transmitted bits
uint8_t bBuzzBeacon = 0; //Bleep once at transmission start, bleep twice at transmission end
uint8_t bLEDBeacon = 0; // flash green led in the same way as BuzzBeacon
uint8_t bLEDRtty = 0;
uint8_t bleepLowBattery = 1;

//=======================================================================================

void(* resetFunc) (void) = 0;
int EEPROM_ADDRESS = 0; //poweroff memory address used for
int EEPROM_VALUE;

char datastring[80]; //buffer for rtty sentence

void setup() {
                  
  pinMode(RADIO_PIN,OUTPUT);
  pinMode(BUZZER_PIN, OUTPUT);
  pinMode(OK_LED, OUTPUT);
  pinMode(WARN_LED, OUTPUT);
  pinMode(GPS_LOCK_LED, OUTPUT);
  pinMode(BATT_VOLTS_PIN, INPUT); //added after, even though it worked without it :S
  pinMode(UVOUT_PIN, INPUT); //uv sensor input
  pinMode(UVOUT_REF_PIN, INPUT); //uv sensor 3v3 reference (using in calculation)


  //WHERE IS VOLTAGE SENSOR PINMODE STATMENT!!!!!!!!!!!!!!!!!!!!!!!!!!!!!!!!!!!!!!!!!!!!!!!!!!!!!!!!!!!!!!!!!!!!!!!!!!!!!
  //why does it work without pinmode
  Serial.begin(9600); //hardware serial for GPS
  mySerial.begin(19200); //software serial for gps debugging

  Wire.begin(); //start I2C (light sensor specific)
  
  if (!BMP280.begin(BMP280_I2C_Address)){
    mySerial.println("No BMP280 found!!");
  }else{
    mySerial.println("BMP280 started sucessfully");
  }

  if (!lightmeter.begin(BH1750::CONTINUOUS_LOW_RES_MODE)){
    mySerial.println("No BH1750 found!!");
  }else{
    mySerial.println("BH1750 started succesfully");
  }

  setupGPS(); //turn off unneeded NMEA messages and change dynamic mode
  mySerial.println("Debugging Started...");
}

void setGPS_DynamicModel6(){ //change dynamic mode of gps to high altitude
  
  int gps_set_sucess=0;

  uint8_t setdm6[] = {
  0xB5, 0x62, 0x06, 0x24, 0x24, 0x00, 0xFF, 0xFF, 0x06,
  0x03, 0x00, 0x00, 0x00, 0x00, 0x10, 0x27, 0x00, 0x00,
  0x05, 0x00, 0xFA, 0x00, 0xFA, 0x00, 0x64, 0x00, 0x5E,
  0x01, 0x00, 0x3C, 0x00, 0x00, 0x00, 0x00, 0x00, 0x00,
  0x00, 0x00, 0x00, 0x00, 0x00, 0x00, 0x84, 0x08 };
  
  while(!gps_set_sucess){
    sendUBX(setdm6, sizeof(setdm6)/sizeof(uint8_t)); //command, sizeofArray
    gps_set_sucess = getUBX_ACK(setdm6);
  }
}

void sendUBX(uint8_t *MSG, uint8_t len) { //rem referencing arrays need pointer dereferencing asterisk
  Serial.flush(); //wait for any existing outgoing transmitted serial data to finish
  Serial.write(0xFF); //255 8bit
  _delay_ms(500);
  
  for(int i=0; i<len; i++) {
    Serial.write(MSG[i]);
    //------
    digitalWrite(WARN_LED, !digitalRead(WARN_LED)); //Pulse the warn LED to show command upload
    digitalWrite(BUZZER_PIN, !digitalRead(BUZZER_PIN)); //pulse the buzzer to indicate upload
    _delay_ms(25); //delay allows the led flashes to be visible
    //-----
 }
}
boolean getUBX_ACK(uint8_t *MSG) {
  uint8_t b;
  uint8_t ackByteID = 0;
  uint8_t ackPacket[10];
  unsigned long startTime = millis();

   // Construct the expected ACK packet
   ackPacket[0] = 0xB5; // header
   ackPacket[1] = 0x62; // header
   ackPacket[2] = 0x05; // class
   ackPacket[3] = 0x01; // id
   ackPacket[4] = 0x02; // length
   ackPacket[5] = 0x00;
   ackPacket[6] = MSG[2]; // ACK class
   ackPacket[7] = MSG[3]; // ACK id
   ackPacket[8] = 0; // CK_A
   ackPacket[9] = 0; // CK_B
 
  // Calculate the checksums
   for (uint8_t ubxi=2; ubxi<8; ubxi++) {
     ackPacket[8] = ackPacket[8] + ackPacket[ubxi];
     ackPacket[9] = ackPacket[9] + ackPacket[8];
   }
 
  while (1) {
   
  // Test for success
   if (ackByteID > 9) {
     // All packets in order!
     //digitalWrite(OK_LED, HIGH);
     mySerial.println("GPS Dynamic mode 6 set successfully (ack recieved)");
     return true;
   }
 
// Timeout if no valid response in 3 seconds
 if (millis() - startTime > 3000) {
  return false;
 }

// Make sure data is available to read
 if (Serial.available()) {
  b = Serial.read();
 
// Check that bytes arrive in sequence as per expected ACK packet
 if (b == ackPacket[ackByteID]) {
  ackByteID++;
 }
 else {
  ackByteID = 0; // Reset and look again, invalid order
 }
 }
 }
}
 
void loop() {

  setBattVoltageVariables(); //having this here stops the buzzer from bleeps because it thinks the voltage level is 0v
  
  if (Serial.available()){

    //mySerial.write(Serial.read()); //uncomment to see if GPS is outputting normal!!
    
    if (gps.encode(Serial.read())){
      if (gps.passedChecksum()){

       if (gps.location.isUpdated() && gps.altitude.isUpdated()){ //only print out if we have non-zero data
         
         GPS_Data_Available = true; //used for gpslock led
         No_GPS_Available_Count =0; //used for gpslock led

            setBMP280Variables(); //set global variable of the BMP280 data
            setBH1750Variables();
            setML8511Variables();
            setGPSVariables(); //set all the global variables to the tinyURL parsed GNGGA info
         
            //resetFunc(); //use to reset the arduino in case of fatal error
       
         if (millis() - RTTY_TX_Prev_Time > TIME_BETWEEN_TX){ //transmit delay for sentences (if any)
          buildTelemetryString();
          RTTY_TX_Prev_Time = millis(); 
         }
         
         // now start using them to build Tx string
         //THIS MUST ONLY BE EXE when we have data avail 
         //i.e it must be inside this if statement or it will not work!!!!!!
  
        //======debugging tinyGPS++ and BMP280 stuff======
          mySerial.print("Lat: ");
          mySerial.print(GPS_Latitude, 6);
          mySerial.print(" Long: ");
          mySerial.print(GPS_Longitude, 6);
          mySerial.print(" GPS_Lock: " );
          mySerial.print(is_GPS_Locked());
          mySerial.print(" Alt: ");
          mySerial.print(GPS_Altitude);
          mySerial.print(" B_Temp: " );
          mySerial.print(BMP280_Temp);
          mySerial.print(" B_Press: ");
          mySerial.print(BMP280_Pressure);
          mySerial.print(" B_Alt: ");
          mySerial.print(BMP280_Altitude);
          mySerial.print(" L_Lux: ");
          mySerial.print(BH1750_Lux);
          mySerial.print(" Batt_Volts: ");
          mySerial.print(Batt_Voltage);
          mySerial.print(" Batt_Perc: ");
          mySerial.print(Get_Battery_Percentage());
          mySerial.print(" UV_Out_Volt: ");
          mySerial.print(UV_Out_Voltage);
          mySerial.print(" UV_Out_Intens: ");
          mySerial.print(UV_Out_Intensity);
          mySerial.println();
         //====================================

        }else{ //if not gps loc and gps alt
          mySerial.print("Waiting for updated GPS values! ("); //debug stuff
          mySerial.print(No_GPS_Available_Count);
          mySerial.print(")");
          mySerial.println();
          No_GPS_Available_Count++; //increment no data counter
          GPS_Data_Available = false;
        }
      }else if (gps.failedChecksum()){
        mySerial.println("Checksum failed"); //debug stuff
      }
    } //gps.encode end
  } //serial avail end

  if (No_GPS_Available_Count >= 5 && No_GPS_Available_Count < NO_GPS_Data_Reset_Thresh){ 
    //check because get no data 5 times row likely means we have lost gps lock
    //it is normal not get data sometimes inbetween serial checks, but not several times in a row.
   digitalWrite(GPS_LOCK_LED, LOW);
  }else if (No_GPS_Available_Count == NO_GPS_Data_Reset_Thresh){
    
    EEPROM_VALUE = EEPROM.read(EEPROM_ADDRESS);
    //READ/WRITE EEPROM sticky variables
    if (EEPROM_VALUE != 0){
      EEPROM.write(EEPROM_ADDRESS, 1);
      //mySerial.println(EEPROM_VALUE);
        if (EEPROM_VALUE == 255)
          EEPROM_VALUE=0; //prevent overflow
          
      //write byte to eeprom to signfy we resetted arduino
      //++addr &= EEPROM.length() - 1; //increment address without overflow
      mySerial.println("Resetting Arduino!!");
      resetFunc();
    }else{
      mySerial.println("Already resetted!");
      No_GPS_Available_Count = 0; //prevents TYPE overlow (255 max)
    }
    
  }else{
    digitalWrite(GPS_LOCK_LED, HIGH);
  }

 
   if (bleepLowBattery && (Get_Battery_Percentage() < Batt_Low_Thresh)){ //make buzzer "blip" when the battery is below 50%

        if (millis() - Batt_Bleep_Prev > Batt_Bleep_Start_Delay){
        digitalWrite(BUZZER_PIN, HIGH);
        delay(50);
        digitalWrite(BUZZER_PIN, LOW);
        Batt_Bleep_Prev = millis();
 
      }
}
  
} //loop end

boolean is_GPS_Locked(){
  if (GPS_Data_Available){ //if there is not data avail we will read outdated vals making it appear as if we do
    return GPS_Satellites >= 4; //4 is needed to get position
  }else{
    return false;
  }
}

float Get_Battery_Percentage(){
  return (Batt_Voltage/Batt_Fully_Charged_Voltage)*100; //output over input
}

void Reset_Arduino(){
  digitalWrite(ARDUINO_RESET_PIN, 0);
}

void setupGPS(){ //turn off unuseful messages (non GCGGA)
  Serial.print("$PUBX,40,GLL,0,0,0,0*5C\r\n");
  delay(100);
  Serial.print("$PUBX,40,ZDA,0,0,0,0*44\r\n");
  delay(100);
  Serial.print("$PUBX,40,VTG,0,0,0,0*5E\r\n");
  delay(100);
  Serial.print("$PUBX,40,GSV,0,0,0,0*59\r\n");
  //delay(100);
  //Serial.print("$PUBX,40,GSA,1,1,1,0*4E\r\n");
  delay(100);
  Serial.print("$PUBX,40,RMC,0,0,0,0*47\r\n");
  delay(100);
  setGPS_DynamicModel6(); //enable GPS flight mode
}

void setML8511Variables(){

  int UV_Level = averageAnalogRead(UVOUT_PIN);
  int UV_Ref_Level = averageAnalogRead(UVOUT_REF_PIN);

  UV_Out_Voltage = 3.3 / UV_Ref_Level * UV_Level;
  UV_Out_Intensity = mapfloat(UV_Out_Voltage, 0.99, 2.9, 0.0, 15.0);
  
  //ref: http://www.theorycircuit.com/arduino-uv-sensor-ml8511/
}

int averageAnalogRead(int pin)
{
  byte rCount = 8;
  uint32_t total = 0; 

  for(int i = 0; i < rCount; i++)
    total += analogRead(pin);
  total /= rCount;

  return(total);  
}


//The Arduino Map function but for floats
//From: http://forum.arduino.cc/index.php?topic=3922.0
float mapfloat(float x, float in_min, float in_max, float out_min, float out_max)
{
  return (x - in_min) * (out_max - out_min) / (in_max - in_min) + out_min;
}

void setBattVoltageVariables(){
  int Batt_Voltage_Raw = analogRead(BATT_VOLTS_PIN);
  Batt_Voltage = map(Batt_Voltage_Raw,0,1023,0,2500)+Batt_Offset;
  Batt_Voltage /= 100;
}

void setBH1750Variables(){
  BH1750_Lux = lightmeter.readLightLevel();
}

void setBMP280Variables(){
  //bmp280
  BMP280_Temp = BMP280.readTemperature();
  BMP280_Pressure = BMP280.readPressure();
  BMP280_Altitude = BMP280.readAltitude(BMP280_Altitude_Pressure_Ref); //1013.25 = sea level pressure/ 1 atmosphere
  //
}

void blinkLED(uint8_t pin, uint8_t num_of_blinks, int blink_delay){
  for (uint8_t i =0; i<= num_of_blinks;i++){
    digitalWrite(pin, HIGH);
    delay(blink_delay);
    digitalWrite(pin, LOW);
    delay(blink_delay);  
  }
}

void setGPSVariables(){ //set the global variables need to build tx string

  GPS_Satellites = gps.satellites.value();
  GPS_Altitude = gps.altitude.meters();
  GPS_Hour = gps.time.hour();
  GPS_Minute = gps.time.minute();
  GPS_Second = gps.time.second();
  GPS_Speed = gps.speed.mph();
  GPS_Course = gps.course.deg();
  GPS_Date = gps.date.value();
  GPS_Latitude = gps.location.lat();
  GPS_Longitude = gps.location.lng();

  //obtain the heading/direction from launch location
  GPS_Course_To_Launch_Location = TinyGPSPlus::courseTo(
  GPS_Latitude,
  GPS_Longitude,
  LAUNCH_LOCATION_LAT,
  LAUNCH_LOCATION_LGN);

  //obtain current distance from launch location
  GPS_Distance_To_Home_In_Miles = TinyGPSPlus::distanceBetween(
  GPS_Latitude, 
  GPS_Longitude, 
  LAUNCH_LOCATION_LAT, 
  LAUNCH_LOCATION_LGN) / (1000.0 * 1.609344); //conv km to miles

  //e.g NW SE SE NE etc.
  GPS_Cardinial = TinyGPSPlus::cardinal(GPS_Course_To_Launch_Location);
  
}

/* probably will used inline or maybe not
int32_t conv_doub_to_int(double input, char resPart){ // convert the decimal lat/long to integer parts that can be charred

    int integerPart = (int)input;
    double decimalPart = fmod(input,1);
    int32_t dPartInt = decimalPart*1000000;
    
   // double num_dec = input - (int)input; //get the decimal part e.g 0.564545
   // double  num_int = input-num_dec; //obtain the integer part
   // double num_dec_res = num_dec*1000000; //bring the decimal into integer (this was a pain to make work)

    return resPart == 0 ? integerPart : dPartInt; //return the int of dec part

}

*/
void buildTelemetryString(){

  int lat_int = (int)abs(GPS_Latitude);
  int32_t lat_dec;
  
  double decimalPart = fmod(GPS_Latitude,1);
  lat_dec = abs(decimalPart)*1000000;              //split the latitude and longitude double into seperate integers
  
  int lon_int = (int)abs(GPS_Longitude);
  int32_t lon_dec;
  
  double decPart = fmod(GPS_Longitude,1);
  lon_dec = abs(decPart)*1000000;

  int batt_int = (int)Batt_Voltage;
  float battDecPart = fmod(Batt_Voltage,1);
  int32_t batt_dec = battDecPart*100;

  int uv_int = (int)UV_Out_Intensity;
  float uvDecPart = fmod(UV_Out_Intensity, 1);
  int32_t uv_dec = uvDecPart*100;

  sprintf(datastring, "$$$RIC,%02d:%02d:%02d,%s%i.%ld,%s%i.%ld,%i,%i,%i,%i,%s,%i,%i,%i,%i,%i.%ld,%i.%ld", 
  GPS_Hour+1, GPS_Minute, GPS_Second, (GPS_Latitude < 0 ? "-" : ""), 
  lat_int, lat_dec, (GPS_Longitude < 0 ? "-" : ""), lon_int, lon_dec, 
  GPS_Satellites,(int)GPS_Speed, (int)GPS_Course, (int)GPS_Course_To_Launch_Location, 
  GPS_Cardinial,(int)BMP280_Temp,(int)BMP280_Pressure, (int)BMP280_Altitude,
  (int)BH1750_Lux, batt_int, batt_dec, uv_int, uv_dec); // Puts the text in the datastring
  
  unsigned int CHECKSUM = gps_CRC16_checksum(datastring);  // Calculates the checksum for this datastring
  char checksum_str[6];
  sprintf(checksum_str, "*%04X\n", CHECKSUM);
  strcat(datastring,checksum_str);
  
  rtty_txstring (datastring);
  
}
 
void rtty_txstring (char * string){
 
  /* Simple function to sent a char at a time to 
    ** rtty_txbyte function. 
    ** NB Each char is one byte (8 Bits)
    */
 
  char c;
 
  c = *string++;
 
  while ( c != '\0'){ //remember all char arrays are terminated with "\0" 
    rtty_txbyte (c);
    c = *string++;
  }
}
 
 
void rtty_txbyte (char c){
  /* Simple function to sent each bit of a char to 
    ** rtty_txbit function. 
    ** NB The bits are sent Least Significant Bit first
    **
    ** All chars should be preceded with a 0 and 
    ** proceded with a 1. 0 = Start bit; 1 = Stop bit
    **
    */
 
 for (int x=0;x<START_BITS;x++){
  rtty_txbit (0); // Start bit
 }
  // Send bits for for char LSB first 
 
  for (int i=0;i<RTTY_ASCII;i++){ // Change this here 7 or 8 for ASCII-7 / ASCII-8
  
    if (c & 1) rtty_txbit(1); 
 
    else rtty_txbit(0); 

    c = c >> 1;
 
  }

 for (int a=0; a<STOP_BITS;a++){
  //rtty_txbit (1); // Stop bit
  rtty_txbit (1); // Stop bit
 }
}
 
void rtty_txbit (int tbit){
  
  if (tbit){
    // high
    digitalWrite(RADIO_PIN, HIGH);
    if (bBuzzRtty) digitalWrite(BUZZER_PIN, HIGH); //beep pcb buzzer in sequence with transmitted bits
    if (bLEDRtty) digitalWrite(OK_LED, HIGH);
  }else{
    // low
    digitalWrite(RADIO_PIN, LOW);
    if (bBuzzRtty) digitalWrite(BUZZER_PIN, LOW); //beep pcb buzzer in sequence with transmitted bits
    if (bLEDRtty) digitalWrite(OK_LED, LOW);
  }  

  if (RTTY_BAUD == 50){
    delayMicroseconds(10000); // For 50 Baud uncomment this and the line below. 
    delayMicroseconds(10150); // You can't do 20150 it just doesn't work as the
  }else if(RTTY_BAUD == 300){ 
    delayMicroseconds(3370); // 300 baud
  }else{
    mySerial.print ("INVALID BAUD RTTY BAUD RATE! USE 50 or 300");
    delayMicroseconds(3370); // 300 baud
  }

}
 
uint16_t gps_CRC16_checksum (char *string){
  size_t i;
  uint16_t crc;
  uint8_t c;
 
  crc = 0xFFFF;
 
  // Calculate checksum ignoring the first two $s
  for (i = 2; i < strlen(string); i++){
    c = string[i];
    crc = _crc_xmodem_update (crc, c);
  }
 
  return crc;
}    

void wait(unsigned long delaytime){ // Arduino Delay doesn't get CPU Speeds below 8Mhz
  
  unsigned long now=millis();
  while((now+delaytime)>=millis()){
    //do nothing
  }
}

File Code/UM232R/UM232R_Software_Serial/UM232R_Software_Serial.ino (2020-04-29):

#include <SoftwareSerial.h>
#include <string.h>
#include <TinyGPS++.h>
#include <math.h>

SoftwareSerial mySerial(5, 4); // RX, TX
TinyGPSPlus gps;

#define BUFFER_SIZE 82


/*STIRK CODE
byte GPSBuffer[BUFFER_SIZE];
byte GPSindex = 0;
*/

unsigned int GPS_Satellites;
unsigned int GPS_Time;
unsigned int GPS_Date;
double GPS_Altitude;
double GPS_Speed;
double GPS_Course;
double GPS_Latitude;
double GPS_Longitude;

//Type in the launch location's GPS coords
const double LAUNCH_LOCATION_LAT = 52.682439; //Telford campus field
const double LAUNCH_LOCATION_LGN = -2.424624; //Telford campus field

//Type in your home location's GPS coords
const double HOME_LOCATION_LAT = 52.592296;
const double HOME_LOCATION_LGN = -2.192684;

int counter = 0;
 
void setup()
{
Serial.begin(9600); //hardware serial
mySerial.begin(9600); //software serial
mySerial.println("Ublox M8Q Data Parsing");
}
 
void loop(){

    if (Serial.available()){

      mySerial.write(Serial.read());
    
      //if (gps.encode(Serial.read())){

       // if (gps.location.isValid()){
        
          //mySerial.print(counter++);
          //mySerial.print(": ");
          //mySerial.println(gps.location.lat(), 6);

          
        //}
      //}
    }
    
  
  /*
  while (Serial.available()){
    if (gps.encode(Serial.read())){
 

/*anthony stike txtstring
    sprintf(txstring, "$$$$$AVA,%i,%02d:%02d:%02d,%s%i.%05ld,%s%i.%05ld,%ld,%d,%i",count, hour, minute, second,lat < 0 ? "-" : "",lat_int,lat_dec,lon < 0 ? "-" : "",lon_int,lon_dec, maxalt,sats,rfm_temp);
    sprintf(txstring, "%s,%i",txstring,errorstatus);
    sprintf(txstring, "%s*%04X\n", txstring, gps_CRC16_checksum(txstring));
    
      if (gps.location.isValid()){
        //http://arduiniana.org/libraries/tinygpsplus/

       GPS_Satellites = gps.satellites.value();
       GPS_Altitude = gps.altitude.meters();
       GPS_Time = gps.time.value();
       GPS_Speed = gps.speed.mph();
       GPS_Course = gps.course.deg();
       GPS_Date = gps.date.value();
       GPS_Latitude = gps.location.lat();
       GPS_Longitude = gps.location.lng();

       double distanceMiles; //obtain current distance from launch location
        distanceMiles = TinyGPSPlus::distanceBetween(
        GPS_Latitude, 
        GPS_Longitude, 
        LAUNCH_LOCATION_LAT, 
        LAUNCH_LOCATION_LGN) / (1000.0 * 1.609344);

       double courseTo; //obtain the heading/direction
        courseTo = TinyGPSPlus::courseTo(
        GPS_Latitude,
        GPS_Longitude,
        LAUNCH_LOCATION_LAT,
        LAUNCH_LOCATION_LGN);

       // mySerial.print("Invalid GPS location");
       
       char* cardinal;
       cardinal = TinyGPSPlus::cardinal(courseTo);
       
      }
      }
    }
    */
  }








  
//checkGPS();
//if (Serial.available()){
//mySerial.write(Serial.read());
//}
//}

void checkGPS(){


  /*anthony stirk code
  int inByte;

  while (Serial.available() > 0){

    inByte = Serial.read();

    if ((inByte=='$') || (GPSindex>=80)){
      GPSindex=0;
    }

    if (inByte != '\r'){
      GPSBuffer[GPSindex++]=inByte;
    }

    if (inByte == '\n'){
      processGPSLine();
      GPSindex=0;
    } 
  }
  */
}

/*
void printGNGGALine(){ //remember it is checking ascii!!!!!!!!!!!!!!

  for (int i = 0; i < BUFFER_SIZE; i++){ //loop through buffer and print each character in sequence
    mySerial.print((char)GPSBuffer[i]); //convert dec to char to get the letter
  }
}

void printGNGGALine(int start, int out){ //remember it is checking ascii!!!!!!!!!!!!!!

  if (out > BUFFER_SIZE)
    out = BUFFER_SIZE;
    
  for (int i = start; i < out; i++){ //loop through buffer and print each character in sequence
    mySerial.print((char)GPSBuffer[i]); //convert dec to char to get the letter
  }
}
*/

/*
void processGPSLine(){

  if ((GPSBuffer[1] == 'G') && (GPSBuffer[2] == 'N') && (GPSBuffer[3] == 'G') && (GPSBuffer[4] == 'G') && (GPSBuffer[5] == 'A')){

    //mySerial.println("GNGGA Detected!");
    
    
    printGNGGALine(); //print the GPSLINE detected this is temp, remove later
    //processGNGGACommand();

    mySerial.println(""); //new line
    mySerial.print("Altitude: ");
    mySerial.print(GPS_Altitude);
    mySerial.print(" ");
    
    mySerial.print("Satellites: ");
    mySerial.print(GPS_Satellites);
    mySerial.print(" ");
    
    mySerial.print("GPS FixMode: ");
    mySerial.print(GPS_FixMode);
    mySerial.print(" ");

    mySerial.print("GPS Time: " ); //UTC time
    //printGNGGALine(7, 11);
    mySerial.print(GPS_Time);

    mySerial.println(""); //new line

    }
  }
*/

/*
void processGNGGACommand(){
  int i, j, k, integerPart;
  unsigned int Altitude;
  
  integerPart = 1;
  GPS_Satellites = 0; //reset global varible
  Altitude=0; //temp local variable

/*
  Sentence structure can be seen at:
  https://www.u-blox.com/en/docs/UBX-13003221 (p123)
  struct: $xxGGA,time,lat,NS,lon,EW,quality,numSV,HDOP,alt,altUnit,sep,sepUnit,diffAge,diffStation*cs<CR><LF>
  a 'quality' of 0 means there is no GPS lock, 1 or 2 means 2D, 3D, Combined GNSS/Dead Reckoning fix
*/
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

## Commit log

2020-04-09 initial commit of existing files
    [Anslem Parts List.xlsm, Flight Tracker.kicad_pcb, Flight Tracker.sch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]
2020-04-11 Made a few symbols and footprints for the BH1750, Ublox8, and BMP280
    [_saved_Flight Tracker.sch]
2020-04-11 Created ML8511, MPU9250_MS5611 symbols and footprints
    [Flight Tracker.sch, _saved_Flight Tracker.sch]
2020-04-12 Attempted to wire the BMP280 correctly cross referencing the datasheet
    [Flight Tracker.sch]
2020-04-13 Removed MPU9250+MS5611 and replaced with just MPU9250. Also created voltage sensor used voltage divide to avoid using the pointless breakout board
    [_saved_Flight Tracker.sch]
2020-04-19 Implemented reverse voltage protection at VIN using FQP47P06 (p-channel mosfet with high gate-drain voltage
    [Flight Tracker.sch, _saved_Flight Tracker.sch]
2020-04-20 Copied the parts list excel document (and updated it with new items) from desktop to laptop
    [OUTDATED_Non-Messed Up Parts List_Macro.xlsm, Part_List_Thesis.xlsm, _OUTDATED_TEMPPP_Non-Messed Up Parts List_Macro.xlsm]
2020-04-21 created footprint for buzzer and corrected it's symbol incorrect wiring
    [Flight Tracker.sch]
2020-04-29 First bit of good progress on transmitting the NMEA messages parsed using tinyGPS++, also added PUBX commands to turn off unwanted NMEA messages as we only care for GNGGA messages for HAB
    [Arduino Uno Board Outline.dxf, Current Consumption of Arduino.xlsx, Flight Tracker.sch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]
2020-05-04 implemented UV sensor, took out carrier shift pot (47k res instead), changed UV_OUT pin, some other stuff, added level shifter for ublox gps tcd and rxd lines, added low voltage detection,\n added no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
    [Current Consumption of Arduino.xlsx, Flight Tracker.sch]
2020-05-06 added ICSP header on PCB, added connector for external thermistor with voltage divider to A3, added connector to tap into I2c bus
    [EDI2CAP.CFG, Flight Tracker.sch, chips.prt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]
2020-05-07 created draft pcb, decided that removing the um232r footprint is required to make the pcb look nicer
    [Flight Tracker.sch, Sheild.kicad_pcb, Sheild.sch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]
2020-05-09 Linked Arduino Nano CAD model from grabcad with footprint, created and linked CAD models for ublox GPS, 5V buzzer, and NTX2B
    [5V Buzzer.step, Arduino Uno Board Outline.dxf, Edge_Mounted_SMA.step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]
2020-05-09 made bmp280 cad model and linked it to pcb, also created sockets for arduino nano
    [BMP280.step, Flight Tracker.kicad_pcb]
2020-05-09 Modified a BH1750 CAD model and linked it with footprint
    [BH1750_Improved.step, CAPC-0603-T0.9-BN.ipt, MPU-9250.iam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]
2020-05-10 Created fuse holder and linked it with footprint
    [Flight Tracker.kicad_pcb, Fuse Holder_w_Fuse.step, ML8511.step]
